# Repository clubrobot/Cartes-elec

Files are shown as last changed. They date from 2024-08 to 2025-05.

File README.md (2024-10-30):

View this project on [CADLAB.io](https://cadlab.io/project/28321). 

# Cartes-elec
Repo de toutes les cartes électroniques utilisées par le CRINSA. Commencé en 2025 sous Kicad 8.0

TODO:
 - Finir le pcb principal
 - Finir le pcb règle
 - Faire le PCB du lidar
 - Faire le PCB du controlleur des afficheurs Leds-Matrix (ou en tout cas le reprogrammer)
 - Faire les 3 PCBs des Superstars

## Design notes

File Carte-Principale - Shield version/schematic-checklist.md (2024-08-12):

# Schematic review checklist

## General

* [x] CAD ERC 100% clean. If some errors are invalid due to toolchain quirks, each exception must be inspected and signed
off as invalid.
* [x] Verify pin numbers of all schematic symbols against datasheet or external interface specification document (if not yet board proven).
* [ ] Schematic symbol matches chosen component package
* [x] Verify pinning of all cables to other boards in the system (straight through vs mirror)

## Passive components
* [x] Power/voltage/tolerance ratings specified as required
* [ ] Ceramic capacitors appropriately de-rated for C/V curve
* [ ] Polarized components specified in schematic if using electrolytic caps etc

## Power supply

### System power input

* [x] Fusing and/or reverse voltage protection at system power inlet
* [ ] TVS at system power inlet
* [ ] Check total input capacitance and add inrush limiter if needed

### Decoupling
* [ ] Decoupling present for all ICs
* [ ] Decoupling meets/exceeds vendor recommendations if specified
* [ ] Bulk decoupling present at PSU

### General
* [x] All power inputs fed by correct voltage
* [x] Check high-power discrete semiconductors and passives to confirm they can handle expected load
* [ ] Analog rails filtered/isolated from digital circuitry as needed

### Errata
* [x] Read errata sheets (if available) for all major devices
* [x] STM32: do not use JTRST pin as an I/O

## Signals

### Digital

* [x] Signals are correct logic level for input pin
* [x] Pullups on all open-drain outputs
* [x] Termination on all high-speed signals
* [x] TX/RX paired correctly for UART, SPI, MGT, etc
* [x] Active high/low enable signal polarity correct

### Strap/init pins
* [x] Pullup/pulldowns on all signals that need defined state at boot -> TODO in Software
* [x] JTAG/ICSP connector provided for all programmable devices

### External interface protection

* [x] Power outputs (USB etc) current limited
* [ ] ESD protection on data lines going off board -> flemme

### Debugging / reworkability

* [ ] Use 0-ohm resistors vs direct hard-wiring for strap pins when possible
* [x] Provide multiple ground clips/points for scope probes
* [x] Dedicated ground in close proximity to analog test points
* [x] Test points on all power rails
* [x] Test points on interesting signals which may need probing for bringup/debug

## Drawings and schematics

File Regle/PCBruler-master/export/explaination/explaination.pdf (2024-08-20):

# PCBruler S - Version 1.0

# 100x32mm / 3,94x1,26in

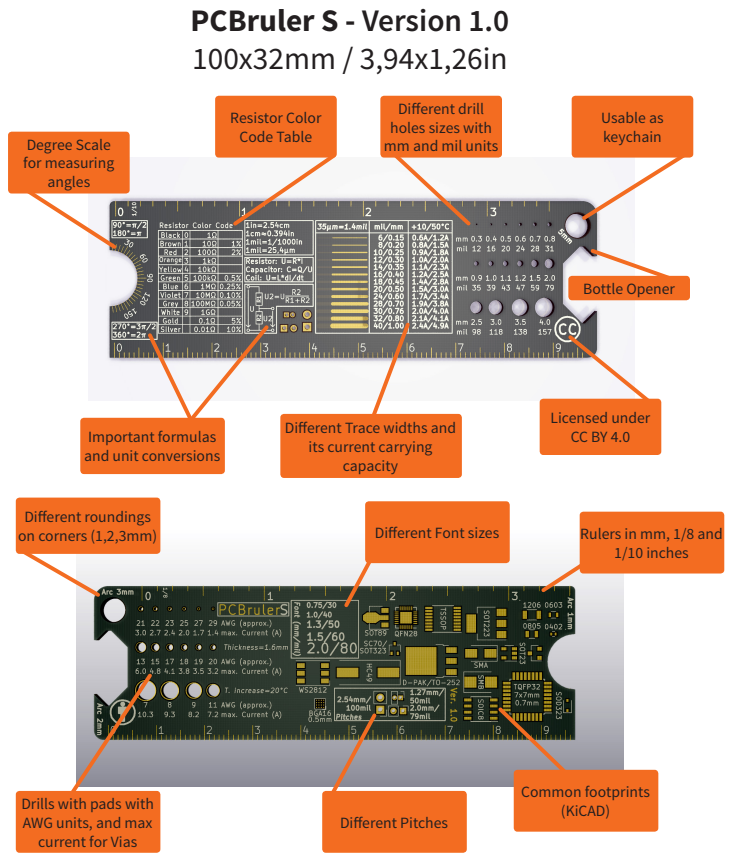
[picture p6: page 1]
Bottle Opener; Degree Scale for measuring angles; Licensed under; Resistor Color Code Table; Usable as keychain; Different roundings on corners (1,2,3mm); Different Pitches; Common footprints (KiCAD); Different Font sizes; Rulers in mm, 1/8 and; 1/10 inches

Different drill
holes sizes with
mm and mil units

CC BY 4.0 Different Trace widths and
its current carrying
capacity

Important formulas
and unit conversions

Drills with pads with
AWG units, and max
current for Vias

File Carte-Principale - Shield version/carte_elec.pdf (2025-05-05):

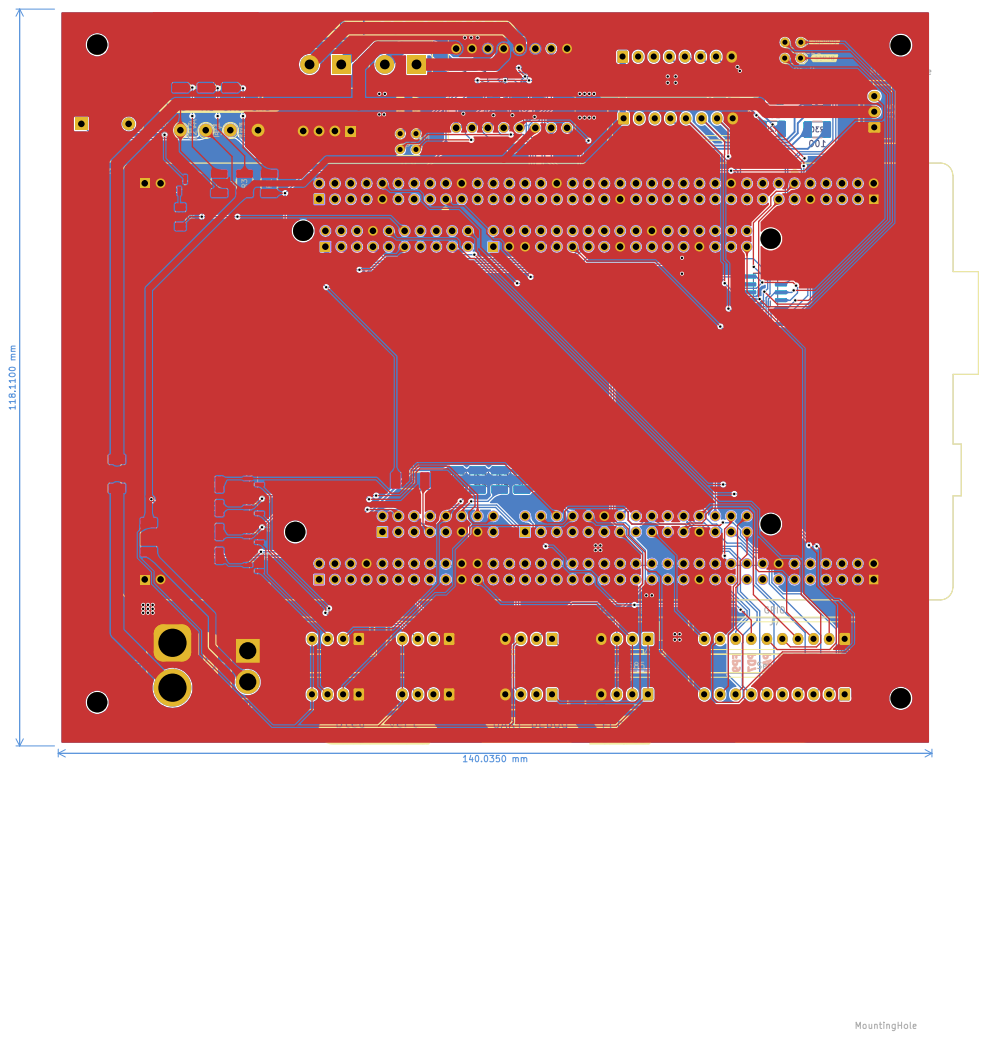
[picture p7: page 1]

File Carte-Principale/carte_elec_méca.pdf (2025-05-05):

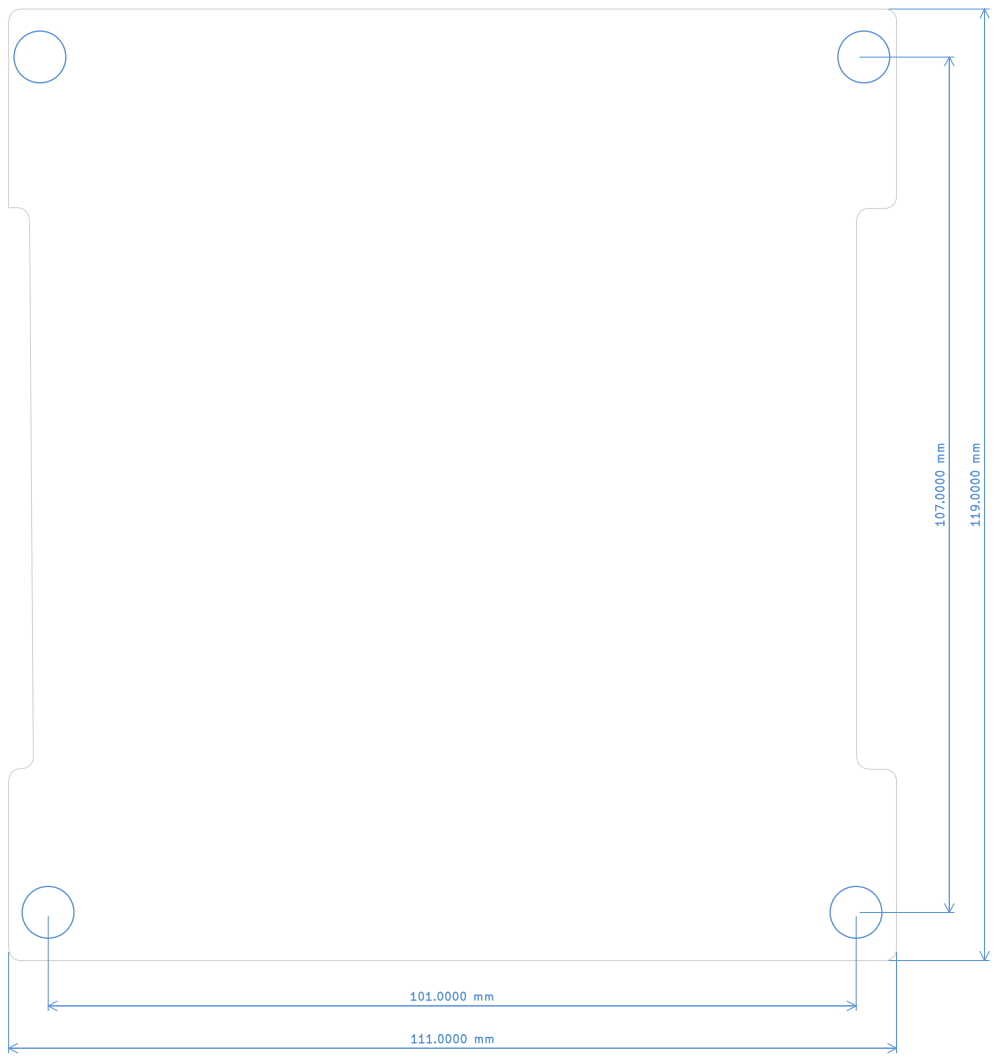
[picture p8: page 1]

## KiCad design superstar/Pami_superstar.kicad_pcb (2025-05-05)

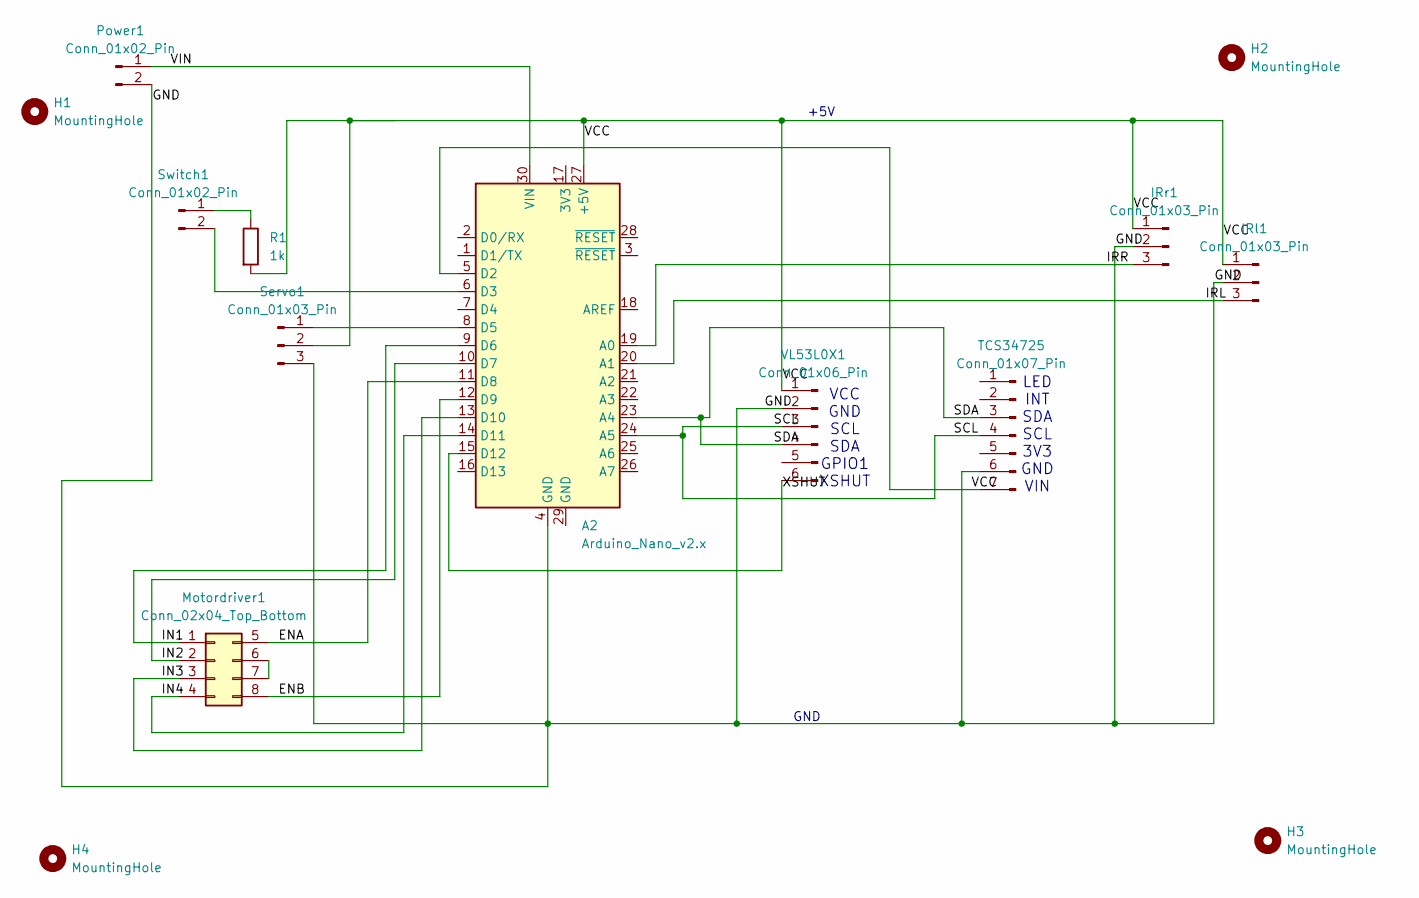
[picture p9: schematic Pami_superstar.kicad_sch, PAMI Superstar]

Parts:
A2: Arduino_Nano_v2.x; Arduino_Nano
H1, H2, H3, H4: MountingHole; MountingHole_3.2mm_M3
IRl1: Conn_01x03_Pin; JST_EH_B3B-EH-A_1x03_P2.50mm_Vertical
IRr1: Conn_01x03_Pin; JST_EH_B3B-EH-A_1x03_P2.50mm_Vertical
Motordriver1: Conn_02x04_Top_Bottom; JST_JWPF_B08B-JWPF-SK-R_2x04_P2.00mm_Vertical
Power1: Conn_01x02_Pin; JST_EH_B2B-EH-A_1x02_P2.50mm_Vertical
R1: 1k; R_Axial_DIN0204_L3.6mm_D1.6mm_P7.62mm_Horizontal
Servo1: Conn_01x03_Pin; JST_EH_B3B-EH-A_1x03_P2.50mm_Vertical
Switch1: Conn_01x02_Pin; JST_EH_B2B-EH-A_1x02_P2.50mm_Vertical
TCS34725: Conn_01x07_Pin; JST_EH_B7B-EH-A_1x07_P2.50mm_Vertical
VL53L0X1: Conn_01x06_Pin; JST_EH_B6B-EH-A_1x06_P2.50mm_Vertical

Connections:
/ENA: A2.11 (D8), Motordriver1.5
/ENB: A2.12 (D9), Motordriver1.8
/GND: A2.4 (GND), IRl1.2, IRr1.2, Power1.2, Servo1.3, TCS34725.6, VL53L0X1.2
/IN1: A2.9 (D6), Motordriver1.1
/IN2: A2.10 (D7), Motordriver1.2
/IN3: A2.13 (D10), Motordriver1.3
/IN4: A2.14 (D11), Motordriver1.4
/IRL: A2.20 (A1), IRl1.3
/IRR: A2.19 (A0), IRr1.3
/SCL: A2.24 (A5), TCS34725.4, VL53L0X1.3
/SDA: A2.23 (A4), TCS34725.3, VL53L0X1.4
/VCC: A2.5 (D2), A2.27 (+5V), IRl1.1, IRr1.1, R1.2, Servo1.2, TCS34725.7, VL53L0X1.1
/VIN: A2.30 (VIN), Power1.1
/XSHUT: A2.15 (D12), VL53L0X1.6
unnamed: A2.6 (D3), Switch1.2
unnamed: A2.8 (D5), Servo1.1
unnamed: Motordriver1.6, Motordriver1.7
unnamed: R1.1, Switch1.1

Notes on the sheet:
LED INT SDA SCL 3V3 GND VIN
VCC GND SCL SDA GPIO1 XSHUT
GND
+5V

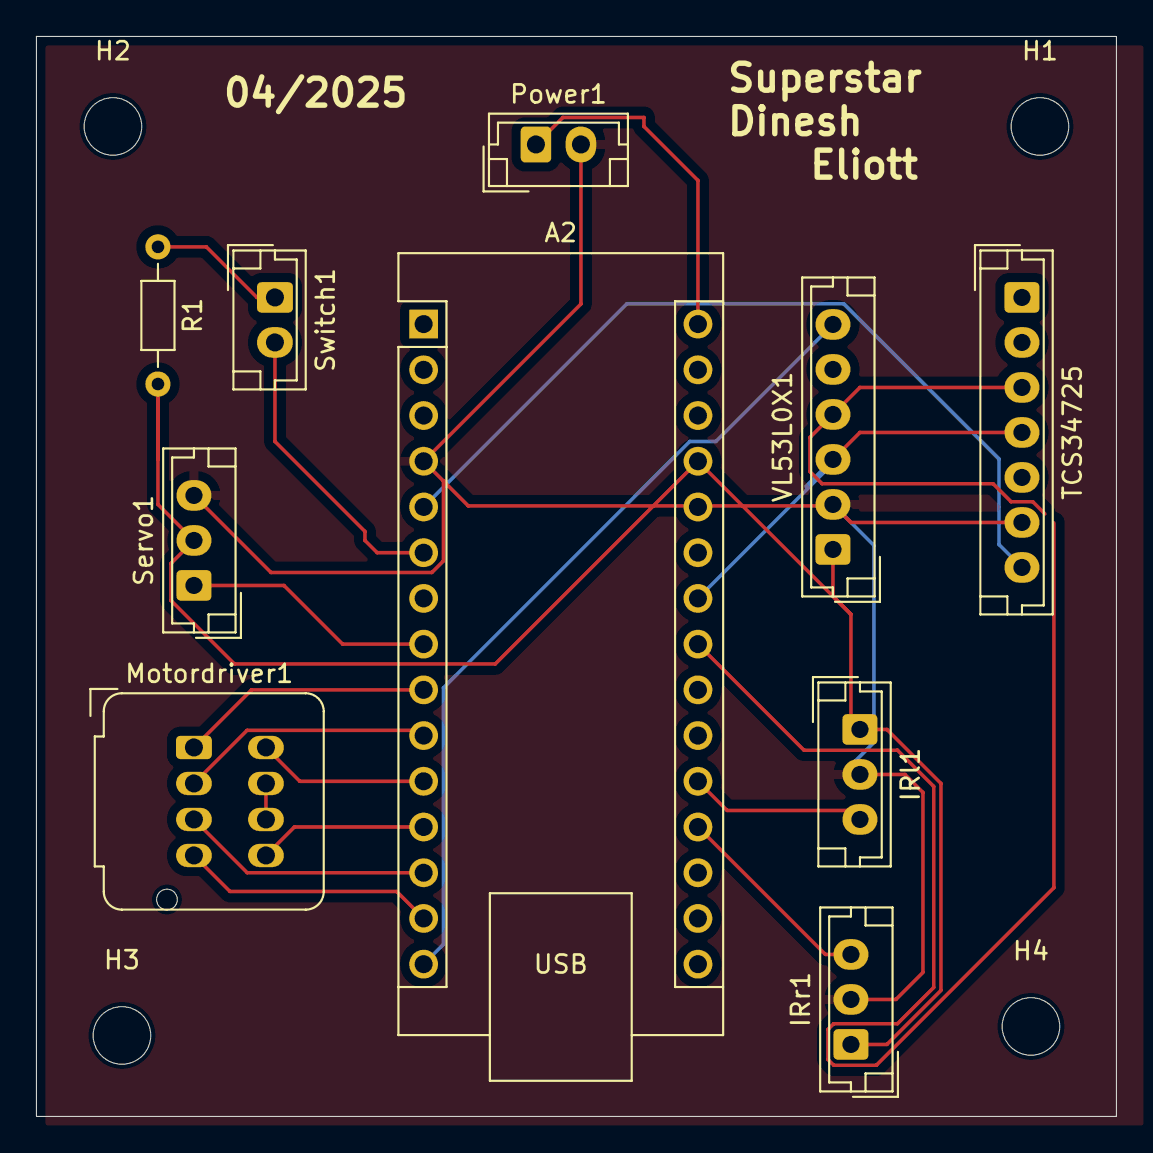
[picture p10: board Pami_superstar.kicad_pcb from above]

Board: 2 copper layers, 60.0 x 60.0 mm, 14 parts (0 on the bottom side), 18 nets.

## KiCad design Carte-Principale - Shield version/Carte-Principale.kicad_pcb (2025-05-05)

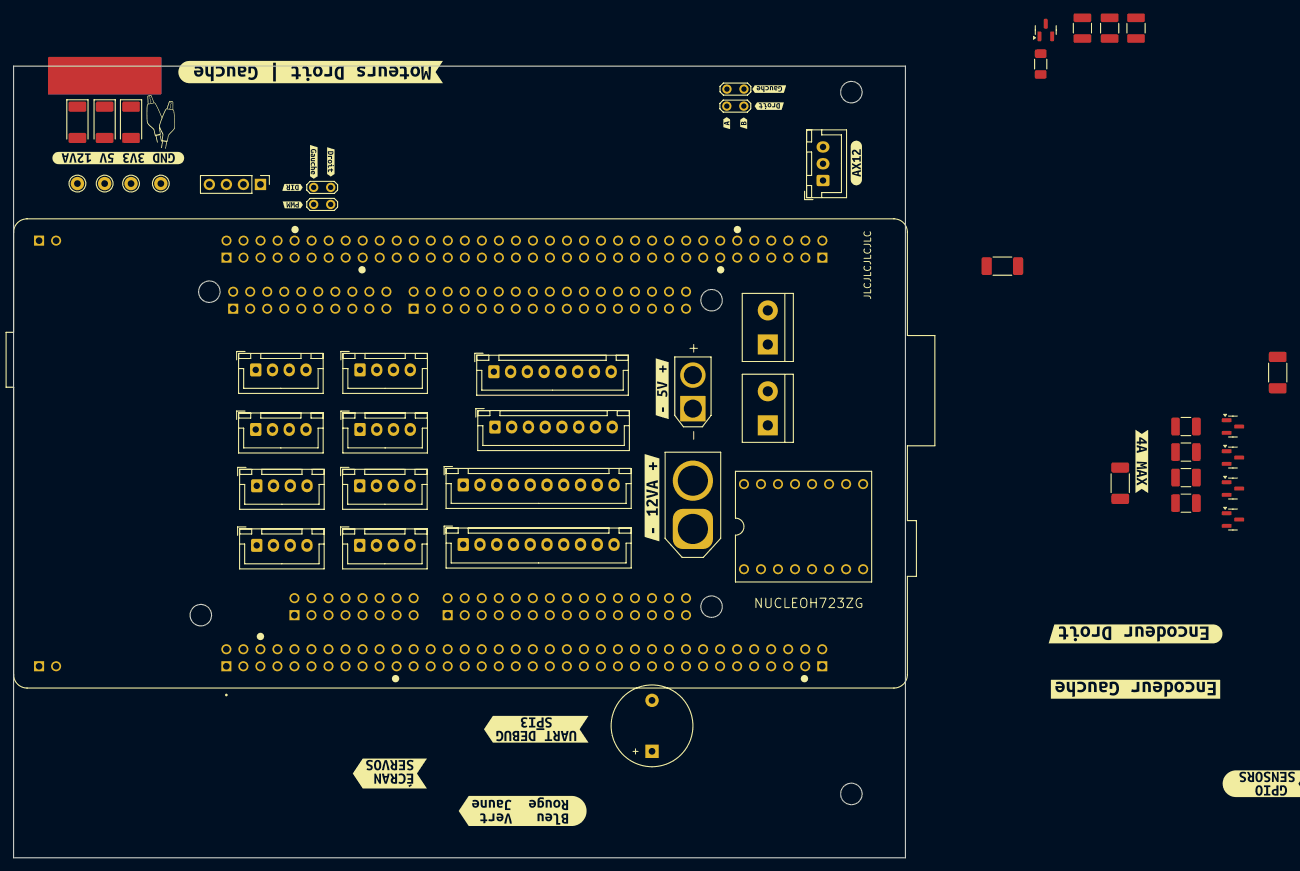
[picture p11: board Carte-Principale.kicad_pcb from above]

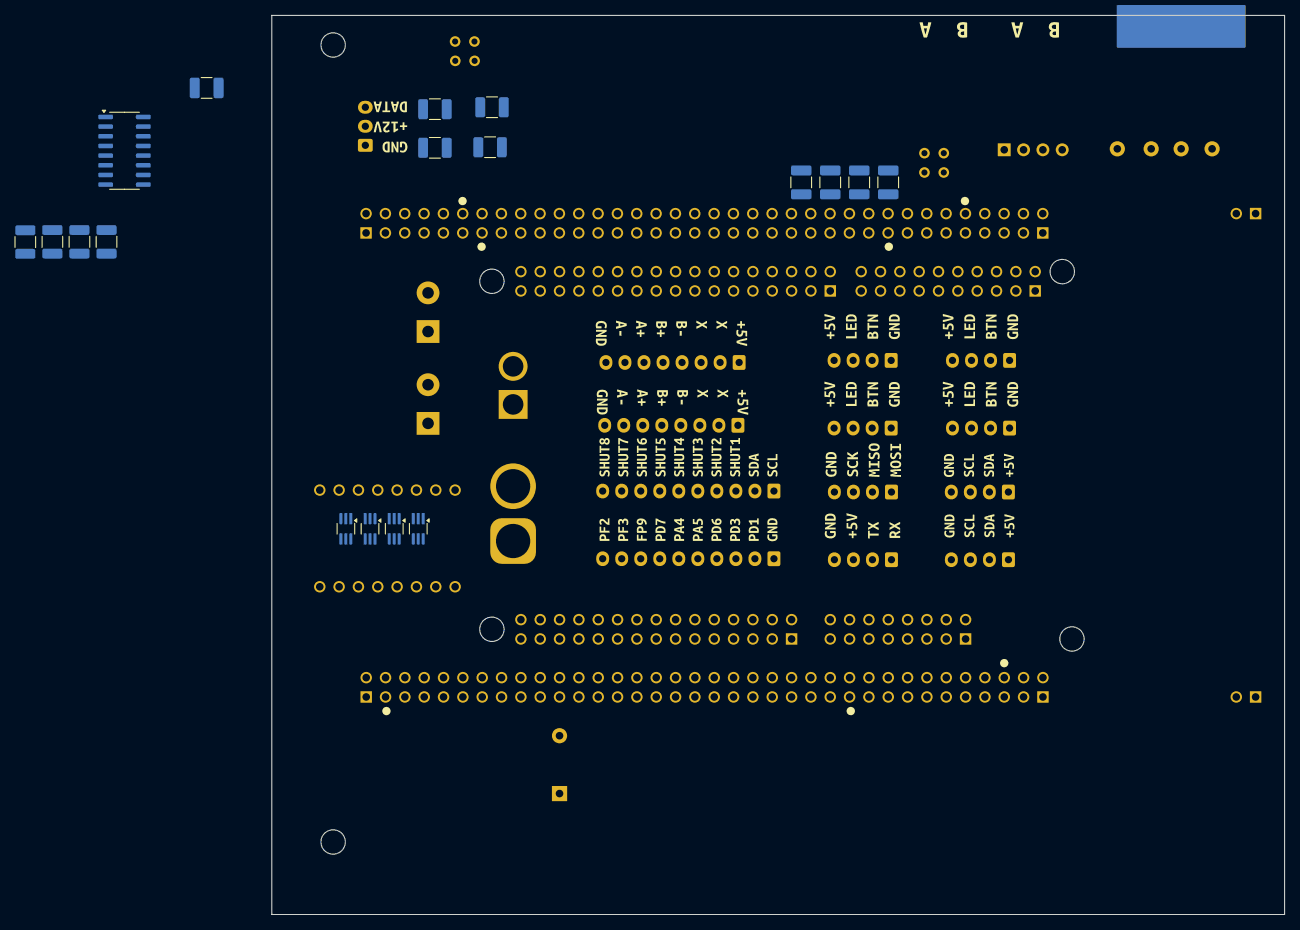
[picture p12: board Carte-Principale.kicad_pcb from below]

Board: 2 copper layers, 133.1 x 118.1 mm, 107 parts (34 on the bottom side), 80 nets, no tracks yet.

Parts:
BZ1: Buzzer; Buzzer_12x9.5RM7.6
C3, C4, C5, C6: 100n; C_1210_3225Metric_Pad1.33x2.70mm_HandSolder
C7: 0.1µ; C_1210_3225Metric_Pad1.33x2.70mm_HandSolder
D5: 5V; LED_2010_5025Metric_Pad1.52x2.65mm_HandSolder
D6: 3V3; LED_2010_5025Metric_Pad1.52x2.65mm_HandSolder
D7: 12VA; LED_2010_5025Metric_Pad1.52x2.65mm_HandSolder
DRV1: DRV8844_BREAKOUT_BOARD
F1, F2: 5A; Fuse_2010_5025Metric_Pad1.52x2.65mm_HandSolder
F3: 1.3A; Fuse_2010_5025Metric_Pad1.52x2.65mm_HandSolder
G1: LOGO
H1, H2, H3, H4: MountingHole; MountingHole_3.2mm_M3
J1: Moteur_Gauche; TerminalBlock_bornier-2_P5.08mm
J2: GND; PinHeader_1x04_P2.54mm_Vertical
J3: 12VA; AMASS_XT60-M_1x02_P7.20mm_Vertical
J4: 5V; AMASS_XT30U-M_1x02_P5.0mm_Vertical
J5: Moteur_Droit; TerminalBlock_bornier-2_P5.08mm
J6: UART_Debug; JST_XH_B4B-XH-A_1x04_P2.50mm_Vertical
J7: GPIO; JST_XH_B10B-XH-A_1x10_P2.50mm_Vertical
J8: Encodeur_D; JST_XH_B8B-XH-A_1x08_P2.50mm_Vertical
J9: SPI3; JST_XH_B4B-XH-A_1x04_P2.50mm_Vertical
J10: Sensors; JST_XH_B10B-XH-A_1x10_P2.50mm_Vertical
J13: Encodeur_G; JST_XH_B8B-XH-A_1x08_P2.50mm_Vertical
J15: AX12; JST_XH_B3B-XH-A_1x03_P2.50mm_Vertical
J18: PCA9685; JST_XH_B4B-XH-A_1x04_P2.50mm_Vertical
J21: I2C Screen; JST_XH_B4B-XH-A_1x04_P2.50mm_Vertical
Q1: BC817; SOT-23
Q2, Q3, Q4, Q5: BSS138; SOT-23
R1, R3, R4: R; R_1210_3225Metric_Pad1.30x2.65mm_HandSolder
R2: R; R_1206_3216Metric_Pad1.30x1.75mm_HandSolder
R9, R10, R11, R12: 10k; R_1210_3225Metric_Pad1.30x2.65mm_HandSolder
R27, R28, R29, R30: 100; R_1210_3225Metric_Pad1.30x2.65mm_HandSolder
R31, R32, R33, R34: 10K; R_1210_3225Metric_Pad1.30x2.65mm_HandSolder
SW1: Rouge; JST_XH_B4B-XH-A_1x04_P2.50mm_Vertical
SW2: Bleu; JST_XH_B4B-XH-A_1x04_P2.50mm_Vertical
SW3: Jaune; JST_XH_B4B-XH-A_1x04_P2.50mm_Vertical
SW4: Vert; JST_XH_B4B-XH-A_1x04_P2.50mm_Vertical
TP1: 3V3; Pin_D1.0mm_L10.0mm
TP2: GND; Pin_D1.0mm_L10.0mm
TP3: 5V; Pin_D1.0mm_L10.0mm
TP5: 12VA; Pin_D1.0mm_L10.0mm
TP6: Test_PWM; TestPoint_2Pads_Pitch2.54mm_Drill0.8mm
TP7: Test_DIR; TestPoint_2Pads_Pitch2.54mm_Drill0.8mm
TP8: Test_Gauche; TestPoint_2Pads_Pitch2.54mm_Drill0.8mm
TP9: Test_Droit; TestPoint_2Pads_Pitch2.54mm_Drill0.8mm
U2: NUCLEOH723ZG; MODULE_NUCLEOH723ZG
U3: AM26LV32xD; SOIC-16_3.9x9.9mm_P1.27mm
U4, U5, U6, U7: 74LVC1G3157; SOT-363_SC-70-6_Handsoldering
kibuzzard-2: G***; kibuzzard-66C478F6
kibuzzard-3: G***; kibuzzard-66C08D4F
kibuzzard-4: G***; kibuzzard-66C08D66
kibuzzard-5: G***; kibuzzard-66C08EFC
kibuzzard-7, kibuzzard-23: G***; kibuzzard-66C09269
kibuzzard-8, kibuzzard-19: G***; kibuzzard-66C0927B
kibuzzard-10: G***; kibuzzard-66C092E0
kibuzzard-22: G***; kibuzzard-66C09293
kibuzzard-24: G***; kibuzzard-66C0929D
kibuzzard-27: G***; kibuzzard-66C0922C
kibuzzard-28, kibuzzard-29: G***; kibuzzard-66C091DE
kibuzzard-30: G***; kibuzzard-66C09044
kibuzzard-34, kibuzzard-37: G***; kibuzzard-66C090AC
kibuzzard-35: G***; kibuzzard-66C09018
kibuzzard-38, kibuzzard-39, kibuzzard-40, kibuzzard-41: G***; kibuzzard-66C08FE4
kibuzzard-66F08110: G***; kibuzzard-66F08110
kibuzzard-66F08121: G***; kibuzzard-66F08121
kibuzzard-66FDA353: G***; kibuzzard-66FDA353
kibuzzard-67548A22: G***; kibuzzard-67548A22
kibuzzard-67548BCB: G***; kibuzzard-67548BCB
kibuzzard-675489B9: G***; kibuzzard-675489B9
kibuzzard-675489F8: G***; kibuzzard-675489F8
kibuzzard-675739BC: G***; kibuzzard-675739BC
kibuzzard-6754898D: G***; kibuzzard-6754898D
kibuzzard-6757392E: G***; kibuzzard-6757392E
kibuzzard-67547681: G***; kibuzzard-67547681
kibuzzard-67548783: G***; kibuzzard-67548783
kibuzzard-67548923: G***; kibuzzard-67548923
kibuzzard-67573990: G***; kibuzzard-67573990

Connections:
+3.3V: C3.2, C4.2, C5.2, C6.2, C7.1, F3.2, R1.1, TP1.1, U3.4 (G), U3.16 (VDD), U4.5 (VCC), U5.5 (VCC), U6.5 (VCC), U7.5 (VCC)
+5V: BZ1.1 (+), DRV1.SLP, F2.2, J6.3, J8.1, J13.1, J18.1, J21.1, R3.1, R31.2, R32.2, R33.2, R34.2, SW1.4 (A), SW2.4 (A), SW3.4 (A), SW4.4 (A), TP3.1, U2.CN11_6 (5V_EXT)
+12VA: DRV1.VMOT, F1.2, J15.2, R4.1, TP5.1
/AX12_RX: J15.3, U2.CN7_1 (D16/I2S_A_MCK), U2.CN7_11 (D21/I2S_B_MCK)
/DEBUG_RX: J6.1, U2.CN11_69 (PD9)
/DEBUG_TX: J6.2, U2.CN12_10 (PD8)
/Encodeur_Droit_A: TP9.1, U2.CN10_11 (A8/ADC_C_IN), U3.3 (1Y)
/Encodeur_Droit_B: TP9.2, U2.CN9_26 (D62/SAI_B_MCLK), U3.5 (2Y)
/Encodeur_Gauche_A: TP8.1, U2.CN12_62 (PF11), U3.11 (3Y)
/Encodeur_Gauche_B: TP8.2, U2.CN12_59 (PF12), U3.13 (4Y)
/Encodeurs/A+_DROITE: J8.6, R27.2, U3.2 (1A)
/Encodeurs/A+_GAUCHE: J13.6, R28.2, U3.10 (3A)
/Encodeurs/A-_DROITE: J8.7, R27.1, U3.1 (1B)
/Encodeurs/A-_GAUCHE: J13.7, R28.1, U3.9 (3B)
/Encodeurs/B+_DROITE: J8.5, R29.2, U3.6 (2A)
/Encodeurs/B+_GAUCHE: J13.5, R30.2, U3.14 (4A)
/Encodeurs/B-_DROITE: J8.4, R29.1, U3.7 (2B)
/Encodeurs/B-_GAUCHE: J13.4, R30.1, U3.15 (4B)
/I2C1_SCL: J18.3, J21.3, U2.CN12_17 (PB6)
/I2C1_SDA: J18.2, J21.2, U2.CN11_21 (PB7)
/I2C2_SCL: J10.1, U2.CN9_19 (D69/I2C_B_SCL)
/I2C2_SDA: J10.2, U2.CN9_21 (D68/I2C_B_SDA)
/Moteurs/IN1: DRV1.IN1, U6.4
/Moteurs/IN2: DRV1.IN2, U7.4
/Moteurs/IN3: DRV1.IN3, U5.4
/Moteurs/IN4: DRV1.IN4, U4.4
/Moteurs/MOTOR1A: DRV1.1A, J1.1
/Moteurs/MOTOR1B: DRV1.1B, J1.2
/Moteurs/MOTOR2A: DRV1.2A, J5.1
/Moteurs/MOTOR2B: DRV1.2B, J5.2
/PA4: J7.6, U2.CN7_17 (D24/SPI_B_NSS)
/PA5: J7.5, U2.CN7_10 (D13/SPI_A_SCK)
/PA6: R2.1, U2.CN7_12 (D12/SPI_A_MISO)
/PA15: DRV1.RST, U2.CN7_9 (D20/I2S_B_WS)
/PB2: J9.1, U2.CN9_13 (D72/COMP1_INP)
/PB12: DRV1.FLT, U2.CN7_7 (D19/I2S_A_WS)
/PB13: DRV1.EN1, U2.CN7_5 (D18/I2S_A_CK)
/PB15: DRV1.EN2, U2.CN7_3 (D17/I2S_A_SD)
/PC8: R32.1, SW3.2, U2.CN8_2 (D43/SDMMC_D0)
/PC9: Q5.1 (G), R12.2, U2.CN8_4 (D44/SDMMC_D1/I2S_A_CKIN)
/PC10: J9.3, U2.CN8_6 (D45/SDMMC_D2)
/PC11: J9.2, U2.CN8_8 (D46/SDMMC_D3)
/PC12: R31.1, SW2.2, U2.CN8_10 (D47/SDMMC_CK)
/PD1: J10.3, U2.CN9_27 (D66/CAN_TX)
/PD2: R33.1, SW4.2, U2.CN8_12 (D48/SDMMC_CMD)
/PD3: J10.10, U2.CN9_10 (D55/USART_B_CTS)
/PD4: R34.1, SW1.2, U2.CN9_8 (D54/USART_B_RTS)
/PD5: Q2.1 (G), R11.2, U2.CN9_6 (D53/USART_B_TX)
/PD6: J7.4, U2.CN9_4 (D52/USART_B_RX)
/PD7: J7.7, U2.CN9_2 (D51/USART_B_SCLK)
/PE0: J7.2, U2.CN10_33 (D34/TIMER_B_ETR)
/PE2: J10.4, U2.CN9_14 (D56/SAI_A_MCLK)
/PE3: J10.5, U2.CN9_22 (D60/SAI_B_SD)
/PE4: J10.6, U2.CN9_16 (D57/SAI_A_FS)
/PE5: J10.7, U2.CN9_18 (D58/SAI_A_SCK)
/PE9: TP6.1, U2.CN10_4 (D6/TIMER_A_PWM1), U4.1, U5.3
/PE11: TP6.2, U2.CN10_6 (D5/TIMER_A_PWM2), U6.3, U7.1
/PF2: J7.10, U2.CN9_17 (D70/I2C_B_SMBA)
/PF3: J7.9, U2.CN7_20 (D8/IO)
/PF4: TP7.2, U2.CN10_7 (A6/ADC_A_IN), U6.6, U7.6
/PF5: TP7.1, U2.CN10_9 (A7/ADC_B_IN), U4.6, U5.6
/PF8: J7.3, U2.CN9_24 (D61/SAI_B_SCK)
/PF9: J7.8, U2.CN9_28 (D63/SAI_B_FS)
/PG0: J10.8, U2.CN9_29 (D65/IO)
/PG1: J10.9, U2.CN9_30 (D64/IO)
/PG2: Q3.1 (G), R10.2, U2.CN8_14 (D49/IO)
/PG3: Q4.1 (G), R9.2, U2.CN8_16 (D50/IO)
GND: C3.1, C4.1, C5.1, C6.1, C7.2, D5.1 (K), D6.1 (K), D7.1 (K), DRV1.GND, DRV1.GND1, J2.1, J2.2, J2.3, J2.4, J3.1, J4.1, J6.4, J7.1, J8.8, J9.4, J13.8, J15.1, J18.4, J21.4, Q1.2 (E), Q2.2 (S), Q3.2 (S), Q4.2 (S), Q5.2 (S), R9.1, R10.1, R11.1, R12.1, SW1.1, SW2.1, SW3.1, SW4.1, TP2.1, U2.CN3_1 (GND_CN3), U2.CN3_2 (GND_CN3), U2.CN4_1 (GND_CN4), U2.CN4_2 (GND_CN4), U2.CN7_8 (GND_CN7), U2.CN8_11 (GND_CN8), U2.CN8_13 (GND_CN8), U2.CN9_12 (GND_CN9), U2.CN9_23 (GND_CN9), U2.CN10_3 (AGND_CN10), U2.CN10_5 (GND_CN10), U2.CN10_17 (GND_CN10), U2.CN10_22 (GND_CN10), U2.CN10_27 (GND_CN10), U2.CN11_8 (GND_CN11), U2.CN11_19 (GND_CN11), U2.CN11_20 (GND_CN11), U2.CN11_22 (GND_CN11), U2.CN11_49 (GND_CN11), U2.CN11_60 (GND_CN11), U2.CN12_9 (GND_CN12), U2.CN12_20 (GND_CN12), U2.CN12_32 (AGND_CN12), U2.CN12_39 (GND_CN12), U2.CN12_54 (GND_CN12), U2.CN12_63 (GND_CN12), U2.CN15_1 (GND_CN15), U2.CN15_2 (GND_CN15), U2.CN16_1 (GND_CN16), U2.CN16_2 (GND_CN16), U3.8 (GND), U3.12 (~G), U4.2 (GND), U4.3, U5.1, U5.2 (GND), U6.1, U6.2 (GND), U7.2 (GND), U7.3
unnamed: BZ1.2 (-), Q1.3 (C)
unnamed: D5.2 (A), R3.2
unnamed: D6.2 (A), R1.2
unnamed: D7.2 (A), R4.2
unnamed: F1.1, J3.2
unnamed: F2.1, J4.2
unnamed: Q1.1 (B), R2.2
unnamed: Q2.3 (D), SW4.3 (K)
unnamed: Q3.3 (D), SW3.3 (K)
unnamed: Q4.3 (D), SW2.3 (K)
unnamed: Q5.3 (D), SW1.3 (K)
unnamed: F3.1, U2.CN8_7 (3V3_CN8)

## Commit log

2024-07-29 Hiérarchie
    [Actionneurs.kicad_sch, Carte-Principale.kicad_pcb, Carte-Principale.kicad_sch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]
2024-07-29 Moteurs + Encodeurs
    [Actionneurs.kicad_sch, Carte-Principale.kicad_sch, Moteurs.kicad_sch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]
2024-07-30 Avancée Actionneur
    [Actionneurs.kicad_sch, Carte-Principale.kicad_sch]
2024-08-01 Rajout écran
    [Actionneurs.kicad_sch, Carte-Principale.kicad_sch, Moteurs.kicad_sch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]
2024-08-12 Schéma vérifié
    [Actionneurs.kicad_sch, Carte-Principale.kicad_pcb, Carte-Principale.kicad_sch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]
2024-08-16 Avancée PCB
    [Actionneurs.kicad_sch, Carte-Principale.kicad_pcb, Carte-Principale.kicad_sch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]
2024-08-20 avancée
    [Actionneurs.kicad_sch, Carte-Principale.kicad_pcb, Carte-Principale.kicad_sch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]
2024-08-23 Final pcb modification
    [Actionneurs.kicad_sch, Carte-Principale.kicad_pcb, Carte-Principale.kicad_sch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]
2024-10-30 Cartes élec à refaire et TODO
    [Actionneurs.kicad_sch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]

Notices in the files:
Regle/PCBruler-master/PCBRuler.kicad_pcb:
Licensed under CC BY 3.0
